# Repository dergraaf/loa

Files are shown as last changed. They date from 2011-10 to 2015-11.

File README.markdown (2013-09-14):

Project Loa
===========

The goal of the project is to develop a powerfull and flexible control board
for robotic (and other) applications.

A microcontroller from the STM32F series from ST is used as the central
processing unit. It is coupled with a Spartan-3 FPGA from Xilinx which will
be used as a powerfull I/O-Expander. With this combination it is possible to
control multiple motors with encoders and other actuators while processing
sensor data and controlling the robot.

For small robots everything will fit into the control board, for big system
the board can act as combined motor controller and sensor preprocessor.
The actual planning etc. can than be outsourced to a faster microcontroller
or PC connected via USB or a fast UART bus.

Naming
------

A "Loa" is a allknowing ghost in Voodoo. The different boards are named
after loas.

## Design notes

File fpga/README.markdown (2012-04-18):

VHDL
====

Structure
---------

File structure goes like this:

    |
    +- modules-\        is for the HDL level code 
    |          |
    |          +- <module name> -\
    |          |                 |
    |                            +- hdl    for HDL sources 
    |                            |
    |                            +- tb     for testbenches
    |
    \- toplevel -\
                 |
                 +- <target> -\
                 |            |
                              +- ISE    ISE Project goes here [^1].
                              |
                              \- ...    implementation files (toplevel.vhd, board.ucf, ..)

[^1]: Only the files really needed like *.xise or *.ise

Naming & Coding Conventions
---------------------------

- All filenames are lower case, names separated by underscores
  - Testbenches end in "_tb.vhd"

- All keywords are lower case!
- Generics are UPPER CASE.

- All signals (except "clk" and "reset") in the port list get the suffix "_p"
- Low active signals should be avoid. If neccessary they get the suffix "_n"
  (or "_np" when they are in the port list).
- Packages get the suffix _pkg

- Always use named association when instantiating sub-modules.

- Use the 'two-process' method whenever possible, see [A structured VHDL design method][two-process]
- Use records types to group associated signals

- Use 3 spaces for indention (Emacs default VHDL style)

[two-process]: www.gaisler.com/doc/vhdl2proc.pdf

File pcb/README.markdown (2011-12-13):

Documentation
=============

Microcontroller selection
-------------------------

For this controller board we wanted to use a Cortex-M3 chip. There are only two
families in wider use at the moment. The STM32F series from ST and the LPC1700
series from NXP.
One goal was that the microcontroller should be be able to control the drive
system of a robot without the FPGA. Therefore it needs to be able to read
four quadrature encoder and control two motors. This leaves only the STM32
series as the LPC1700 features only one quadrature encoder.

Currently there are four different strains within the STM32 series available.
The STM32F103 was the first one. A lot of development boards use controllers
from this series. But it has a quite long and annoying Errata Sheet, some
peripherals don't work with each other. Most important it is not possible to
use CAN and USB at the same time because they share an internal buffer.
After the 103er the 105/107er arrived. Their most important feature is that it
is possible to use CAN and USB at the same time. Some other stuff like the
ethernet interface are not important for us. The peripherals are improved,
leading to a shorter Errata Sheet. Their only drawback comparted to the 103er
series is that they are limited to 256kB Flash compared to a maximum of
1024kB for the 103er. The 256kB Flash might just be to few for the desired
application as a robot controller.

In the last time two new strains appeared. The STM32F200- and the
STM32F400-series. They are improvments of the 105/107er with a slightly
different pinout. Some of the power pins need to be connected differently, all
of the IO-Pins remain the same. Therefore it is possible to create a board
which supports STM32F1xx and STM32F2xx through some solder jumpers.
The STM32F207 are a bit faster (120MHz instead of 72MHz) and provide more Flash
memory (up to 1024kB). The STM32F407 uses an Cortex-M4 instead of the Cortex-M3
of all the other devices. With 150MHz and an integrated FPU it should be again
faster, especially for floating point calculations. The STM32F4xx are pin
compatible to the STM32F2xx.

As the STM32F4xx are to new and are not yet available from distributors like
Farnell we choose the STM32F207. This leaves the options of an upgrade to a
STM32F407 later.

STM32F207
---------

Pin  | Alternate Functions      | Usage on the Board         | Proposed Usage
---- | ------------------------ | -------------------------- | ----------------
PA0  | ADC0/Timer 2.1/Timer 5.1 |                            | Encoder 1
PA1  | ADC1/Timer 2.2/Timer 5.2 |                            | Encoder 1
PA2  | ADC2/Timer 9.1           |                            |     - 
PA3  | ADC3/Timer 9.2           |                            |     - 
PA4  | SPI1 Cs                  | -> FPGA (DIN)              | 
PA5  | SPI1 Sck                 | -> FPGA                    | 
PA6  | SPI1 Miso                | <- FPGA                    | 
PA7  | SPI1 Mosi                | -> FPGA                    | 
PA8  |                          | <- FPGA                    | 
PA9  | USB Vbus                 | <- USB                     | 
PA10 | USB ID                   | <- USB                     | 
PA11 | USB DM                   | <> USB                     | 
PA12 | USB DP                   | <> USB                     | 
PA13 | TMS                      | <- JTAG                    | 
PA14 | TCK                      | <- JTAG                    | 
PA15 | TDI                      | <- JTAG                    | 
---- | ------------------------ | -------------------------- | ----------------
PB0  | ADC8/Timer 3.3           |                            |     - 
PB1  | ADC9/Timer 3.4           |                            |     - 
PB2  | (BOOT1)                  | FPGA_CCLK                  | 
PB3  | TDO                      | -> JTAG                    | 
PB4  | Timer 3.1/TRST           |                            | Encoder 2
PB5  | Timer 3.2                |                            | Encoder 2
PB6  | UART1 Tx                 |                            | -> Upstream
PB7  | UART1 Rx                 |                            | <- Upstream
PB8  | I2C1 Scl                 |                            |     - 
PB9  | I2C1 Sda                 |                            |     - 
PB10 | I2C2 Scl                 |                            |     - 
PB11 | I2C2 Sda                 |                            |     - 
PB12 | SPI2 Cs /CAN2 Rx         |                            |     - 
PB13 | SPI2 Sck/CAN2 Tx         |                            |     - 
PB14 | SPI2 Miso                |                            |     - 
PB15 | SPI2 Mosi                |                            |     - 
---- | ------------------------ | -------------------------- | ----------------
PC0  | ADC10                    |                            |     - 
PC1  | ADC11                    |                            |     - 
PC2  | ADC12                    |                            |     - 
PC3  | ADC13                    |                            |     - 
PC4  | ADC14                    |                            |     - 
PC5  | ADC15                    |                            |     - 
PC6  | Timer 3.1/Timer 8.1      |                            | Encoder 3
PC7  | Timer 3.2/Timer 8.2      |                            | Encoder 3
PC8  | Timer 3.3/Timer 8.3      |                            |     - 
PC9  | Timer 3.4/Timer 8.4      |                            |     - 
PC10 | UART4 Tx                 |                            | SAB (Sensor Actor Bus)
PC11 | UART4 Rx                 |                            | SAB (       "        )
PC12 | UART5 Tx                 |                            | -> Debug UART
PC13 | (nur als Eingang)        | <- Button 1                | 
PC14 | (nur als Eingang)        | <- FPGA (DONE)             | 
PC15 | (nur als Eingang)        | <- SD Card Detect          | 
---- | ------------------------ | -------------------------- | ----------------
PD0  | CAN1 Rx                  | <- CAN                     | 
PD1  | CAN1 Tx                  | -> CAN                     | 
PD2  | UART5 Rx                 |                            | <- Debug UART
PD3  |                          | -> SD Card (CS)            | 
PD4  |                          |                            |     - 
PD5  | UART2 Tx                 |                            | SPI 1
PD6  | UART2 Rx                 |                            | SPI 1
PD7  | UART2 Ck                 |                            | SPI 1
PD8  | UART3 Tx                 | -> SD Card/Dataflash       | 
PD9  | UART3 Rx                 | <- SD Card/Dataflash       | 
PD10 | UART3 Ck                 | -> SD Card/Dataflash       | 
PD11 |                          | -> Dataflash (CS)          | 
PD12 | Timer 4.1                |                            | Encoder 4
PD13 | Timer 4.2                |                            | Encoder 4
PD14 | Timer 4.3                |                            |     - 
PD15 | Timer 4.4                |                            |     - 
---- | ------------------------ | -------------------------- | ----------------
PE0  |                          | -> FPGA (CCLK)             | 
PE1  |                          | -> FPGA (PROG_B)           | 
PE2  |                          | -> FPGA                    | 
PE3  |                          | -> LED0                    | 
PE4  |                          | -> LED1                    | 
PE5  | Timer 9.1                | -> LED2                    | 
PE6  | Timer 9.2                | -> LED3                    | 
PE7  |                          | <- FPGA (INIT_B)           | 
PE8  | Timer 1.1N               |                            | Motor 1
PE9  | Timer 1.1                |                            | Motor 1
PE10 | Timer 1.2N               |                            | Motor 2
PE11 | Timer 1.2                |                            | Motor 2
PE12 | Timer 1.3N               |                            |     - 
PE13 | Timer 1.3                |                            |     - 
PE14 | Timer 1.4                |                            |     - 
PE15 |                          |                            |     - 

#### Peripherals

- 2x Motor (Timer 1)
- 4x Encoder (Timer 3+4+5+8)

- 1x Upstream (Uart 1)
- 1x Debug (Uart 5)
- 2x SPI (Uart2+SPI2)
- 1x Peripheral UART (Uart 4)

#### SPI vs. SDIO

We choose a SPI over the SDIO interface for the SD Card because SDIO would
have blocked UART4 and UART5.

#### JTAG Connector

This is the official JTAG Connector proposed by ARM for the Cortex-M3. The only
difference is that we don't use a 1.27mm grid but a normal 2.54mm one. This
allows to use standard ribbon cable.

            ------
    3.3V --| 1  2 |-- TMS
     GND --| 3  4 |-- TCLK
     GND -[| 5  6 |-- TDO
    RTCK --| 7  8 |-- TDI
     GND --| 9 10 |-- Reset (SRST)
            ------

On this connector TRST (also called NJTRST) is not connected. This might
lead to the problem that the "reset halt" command from OpenOCD doesn't work.

RTCK is only used for ARM7 devices, so it is left open here.

FPGA Spartan-3
--------------

The Spartan-3 was choosen because it was the only FPGA from all the Spartan-3
Series (3,3E,3A,3AN) that is available in TQFP144 package from Reichelt or
Farnell.

The XC3S50A and XC3S50AN are also available, but the bigger packages are not.

### Pins

Unused pins are defined as inputs with pull-downs by default. Can be changed
by primitives or constraints in the bitstream generation.

All user-I/O pins, input-only pins, and dual-purpose pins that are not actively
involved in the currently-selected configuration mode are high impedance
(floating, three-stated, Hi-Z) during the configuration process.

### Configuration of the FPGA

DONE
:   Output with 2,5V supply. Driven low during configuration. Goes high after
    configuration has finished.

PROG_B
:   Input with 2,5 supply. Low pulse (>= 500ns) restarts the configuration
    process.

CCLK
:   Input with 2,5 supply in slave modes. Configuration clock.

DIN
:   Serial Mode input

DOUT
:   Serial Data Output. Not used in single FPGA designs.

INIT_B
:   Output with 3,3V supply. Driven low during before configuration. After it
    goes high the M[2:0] pins are sampled and the configuration is started.
    Holding the pin low stalls the configuration start. During configuration
    the FPGA indicates the occurrence of a configuration
    data error (i.e., CRC error) by asserting INIT_B Low.
    After configuration successfully completes, i.e., when the DONE pin goes
    High, the INIT_B pin is available as a full user-I/O pin.

HSWAP_EN 
:   When the pin is Low, each pin (not only the configuration pins) has an
    internal pull-up resistor that is active throughout configuration, starting
    immediately on power-up.

M[2:0]
:   Select the configuration mode.
    '111' Slave Serial Mode
    '101' JTAG Mode

#### Spartan 3 Bitstream Size

Device  | Configuration
        |  Size [Bits]
------- | --------------
XC3S50  |     439,264
XC3S200 |   1,047,616
XC3S400 |   1,699,136

### Power Supply

http://focus.ti.com/analog/docs/refdesignovw.tsp?familyId=64&contentType=2&genContentId=34823

For the XC3S250E:
- 1.2V at 1A
- 2.5V at 0.15A
- 3.3V at 3A

For the XC3S500E
- 1.2V at 1.5A
- 2.5V at 0.15A
- 3.3V at 3A

The XC3S200/400 should be somewhere in between, the XC3S50 significantly lower.

### JTAG Connector

The JTAG connector is a stripped down version of the original connector from
the Xilinx Parallel Cable IV. Original it uses 14 pins, but we leave the last
four pins out to fit it to a standard 10 pin header. These pins are only used
for programming the FPGA via Slave Serial mode through the PC so no
functionality is lost.

           ------
    GND --| 1  2 |-- Vref (connect to Vaux)
    GND --| 3  4 |-- TMS
    GND -[| 5  6 |-- TCK
    GND --| 7  8 |-- TDO
    GND --| 9 10 |-- TDI
           ------

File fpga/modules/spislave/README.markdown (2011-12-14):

The SPI Slave module has two responsibilities:
- Decoding the SPI protocol
- Busmaster for the internal bus

Protocol
--------

All transfers (address and data) are 16-bit. First the address is written.
The MSB determines wether the folowing transfer is a read (MSB = '0') or write (MSB = '1')
transfer.

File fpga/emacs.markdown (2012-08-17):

Emacs
=====

Install Emacs via:

    $ sudo apt-get install emacs

Commands
--------
 
C => Strg  
M => Alt  

C-c C-b		Beautify Buffer  
C-w 		Cut Text  
M-w			Copy Text  
C-y			Paste Text  
C-space		Set mark  
C-x C-s		Save File  
C-X u		Undo

C-c C-p C-w		Copy entity or component
C-c C-p C-c		Paste as component
C-c C-p C-i		Paste as instance
C-c C-p C-s		Paste as signals

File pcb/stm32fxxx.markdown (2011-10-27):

Pin Assignment
==============

STM32F207
---------

Pin  |  ADC  |    Timer    |   UART   |    SPI    | 
---- | ----- | ----------- | -------- | --------- | 
PA0  | ADC0  | Timer 2/5.1 |          |           | 
PA1  | ADC1  | Timer 2/5.2 |          |           | 
PA2  | ADC2  | Timer 9.1   |          |           | 
PA3  | ADC3  | Timer 9.2   |          |           | 
PA4  |       |             |          | SPI1 Cs   | 
PA5  |       |             |          | SPI1 Sck  | 
PA6  |       |             |          | SPI1 Miso | 
PA7  |       |             |          | SPI1 Mosi | 
PA8  |       |             |          |           | 
PA9  |       |             |          |           | USB Vbus
PA10 |       |             |          |           | USB ID
PA11 |       |             |          |           | USB DM
PA12 |       |             |          |           | USB DP
PA13 |       |             |          |           | TMS
PA14 |       |             |          |           | TCK
PA15 |       |             |          |           | TDI

PB0  | ADC8  | Timer 3.3   |          |           | 
PB1  | ADC9  | Timer 3.4   |          |           | 
PB2  |       |             |          |           | 
PB3  |       |             |          |           | TDO
PB4  |       | Timer 3.1   |          |           | TRST
PB5  |       | Timer 3.2   |          |           | 
PB6  |       |             | UART1 Tx |           | 
PB7  |       |             | UART1 Rx |           | 
PB8  |       |             |          |           | I2C1 Scl
PB9  |       |             |          |           | I2C1 Sda
PB10 |       |             |          |           | I2C2 Scl
PB11 |       |             |          |           | I2C2 Sda
PB12 |       |             |          | SPI2 Cs   | CAN2 Rx
PB13 |       |             |          | SPI2 Sck  | CAN2 Tx
PB14 |       |             |          | SPI2 Miso | 
PB15 |       |             |          | SPI2 Mosi | 

PC0  | ADC10 |             |          |           | 
PC1  | ADC11 |             |          |           | 
PC2  | ADC12 |             |          |           | 
PC3  | ADC13 |             |          |           | 
PC4  | ADC14 |             |          |           | 
PC5  | ADC15 |             |          |           | 
PC6  |       | Timer 3/8.1 |          |           | 
PC7  |       | Timer 3/8.2 |          |           | 
PC8  |       | Timer 3/8.3 |          |           | 
PC9  |       | Timer 3/8.4 |          |           | 
PC10 |       |             | UART4 Tx |           | 
PC11 |       |             | UART4 Rx |           | 
PC12 |       |             | UART5 Tx |           | 
PC13 |       |             |          |           | (nur als Eingang)
PC14 |       |             |          |           | (nur als Eingang)
PC15 |       |             |          |           | (nur als Eingang)

PD0  |       |             |          |           | CAN1 Rx
PD1  |       |             |          |           | CAN1 Tx
PD2  |       |             | UART5 Rx |           | 
PD3  |       |             |          |           | 
PD4  |       |             |          |           | 
PD5  |       |             | UART2 Tx |           | 
PD6  |       |             | UART2 Rx |           | 
PD7  |       |             | UART2 Ck |           | 
PD8  |       |             | UART3 Tx |           | 
PD9  |       |             | UART3 Rx |           | 
PD10 |       |             | UART3 Ck |           | 
PD11 |       |             |          |           | 
PD12 |       | Timer 4.1   |          |           | 
PD13 |       | Timer 4.2   |          |           | 
PD14 |       | Timer 4.3   |          |           | 
PD15 |       | Timer 4.4   |          |           | 

PE0  |       |             |          |           | 
PE1  |       |             |          |           | 
PE2  |       |             |          |           | 
PE3  |       |             |          |           | 
PE4  |       |             |          |           | 
PE5  |       | Timer 9.1   |          |           | 
PE6  |       | Timer 9.2   |          |           | 
PE7  |       |             |          |           | 
PE8  |       | Timer 1.1N  |          |           | 
PE9  |       | Timer 1.1   |          |           | 
PE10 |       | Timer 1.2N  |          |           | 
PE11 |       | Timer 1.2   |          |           | 
PE12 |       | Timer 1.3N  |          |           | 
PE13 |       | Timer 1.3   |          |           | 
PE14 |       | Timer 1.4   |          |           | 
PE15 |       |             |          |           |

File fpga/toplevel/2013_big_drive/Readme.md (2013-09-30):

Configuration Workflow
======================

FPGA connected by JTAG
----------------------

	 VHDL Files, UCF Files
	  |
	  | Xilinx ISE: xst, ngdbuild, map, par, trce, bitgen
	  v
	 ise/toplevel.bit
	  |
	  | Xilinx ISE: impact -batch impact.cmd
	  v
	 ise/toplevel.svf
	  |
	  | UrJTAG: jtag urjtag.cmd
	  v
	 FPGA per JTAG
	 
Configure FPGA by STM32
-----------------------

The configuration must be stored into the external flash. 
There is a java tool

	 VHDL Files, UCF Files
	  |
	  | Xilinx ISE: xst, ngdbuild, map, par, trce, bitgen
	  v
	 ise/toplevel.bit
	  |
	  | 
	  v

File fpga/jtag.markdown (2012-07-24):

Programming an FPGA
===================

The result of the implementation with the synthesis tools from Xilinx is a bit-file. 
This bit-file must be programmed into the FPGA. This can be done by various means:

*   JTAG
*   Platform Flash
*   Microcontroller

See Xilinx documentation for details. Here programming the FPGA using the JTAG port
is describe. Two different tools are tested: UrJtag and xc3sprogram. Both were used 
with the busblaster v2 hardware. 

Using UrJtag
------------

See http://urjtag.sourceforge.net/

### Generate a SVF File

Create a new file called "impact.cmd" with the following content:

    setMode -bs
    setCable -port svf -file toplevel.svf
    addDevice -p 1 -file path/to/your/bitfile.bit
    program -p 1
    closeCable
    quit

Now run impact to create a SVF file:

    $ impact -batch impact.cmd

If the 'impact' command isn't found check that the ISE path is added to PATH.
For example add the following to ~/.bashrc (adapt it your ISE-path):
    export PATH=$PATH:/home/user/fpga/xilinx_ise/ISE_DS/ISE/bin/lin/

### Download and Install

get UrJtag at http://sourceforge.net/projects/urjtag/files/latest/download?source=files

    $ cd urjtag-0.10
    $ ./configure --with-libftdi --enable-lowlevel=ftdi
    $ make
    $ sudo make install

you can also use the git repository:

    $ git clone git://urjtag.git.sourceforge.net/gitroot/urjtag/urjtag urjtag
    $ cd urjtag/urjtag
    $ sudo apt-get install autoconf autopoint libtool libusb-dev libftdi-dev python-dev flex bison
    $ autoreconf -i -s -v -f
    $ ./configure
    $ make
    $ sudo make install

And for Ubuntu users:

    $ sudo su
    $ echo "/usr/local/lib" > /etc/ld.so.conf.d/other.conf
    $ ldconfig
    $ exit

### Connect to your FPGA

    $ jtag
    jtag> cable jtagkey vid=0x0403 pid=0x6010 driver=ftdi-mpsse
    Connected to libftdi driver.
    jtag> detect
    IR length: 6
    Chain length: 1
    Device Id: 00000001010000011100000010010011 (0x000000000141C093)
      Manufacturer: Xilinx
      Part(0):         xc3s400
      Stepping:     0
      Filename:     /usr/local/share/urjtag/xilinx/xc3s400/xc3s400
    jtag> 

### Program the FPGA

    jtag> svf toplevel.svf
    jtag> 

xc3sprog
--------

The benefit of xc3sprog is that it is not necessary to run Xilinx Impact. 
xc3sprog can write bit-files directly to FPGA. 

### Get the latest xc3sprog

The precompiled version did not work. You need cmake and libftdi-dev. 

    $ svn co https://xc3sprog.svn.sourceforge.net/svnroot/xc3sprog xc3sprog

Create a new build directory and dive into

    $ mkdir xc3sprog/build
    $ cd    xc3sprog/build
    $ cmake ../trunk
    $ make

### Test the tool

Now xc3sprog is ready. Make sure you can access the USB device. Adjust 
permissions of /dev/bus/usb/00?/0??.

   $  ./xc3sprog -c bbv2 -j

will show something like

    XC3SPROG (c) 2004-2011 xc3sprog project $Rev: 674 $ OS: Linux
    Free software: If you contribute nothing, expect nothing!
    Feedback on success/failure/enhancement requests:
        http://sourceforge.net/mail/?group_id=170565 
    Check Sourceforge for updates:
        http://sourceforge.net/projects/xc3sprog/develop
    
    Using Libftdi, 
    JTAG loc.:   0  IDCODE: 0x01414093  Desc:                        XC3S200 Rev: A  IR length:  6
    JTAG loc.:   1  IDCODE: 0x05045093  Desc:                         XCF02S Rev: A  IR length:  8

### Write to FPGA

This was a test using the Digilent Spartan 3 Development board. You can write
a bit-file to the FPGA (or with -p 1 to the platform flash) using:

    $ ./xc3sprog -c bbv2 /path/to/your/bitfile.bit

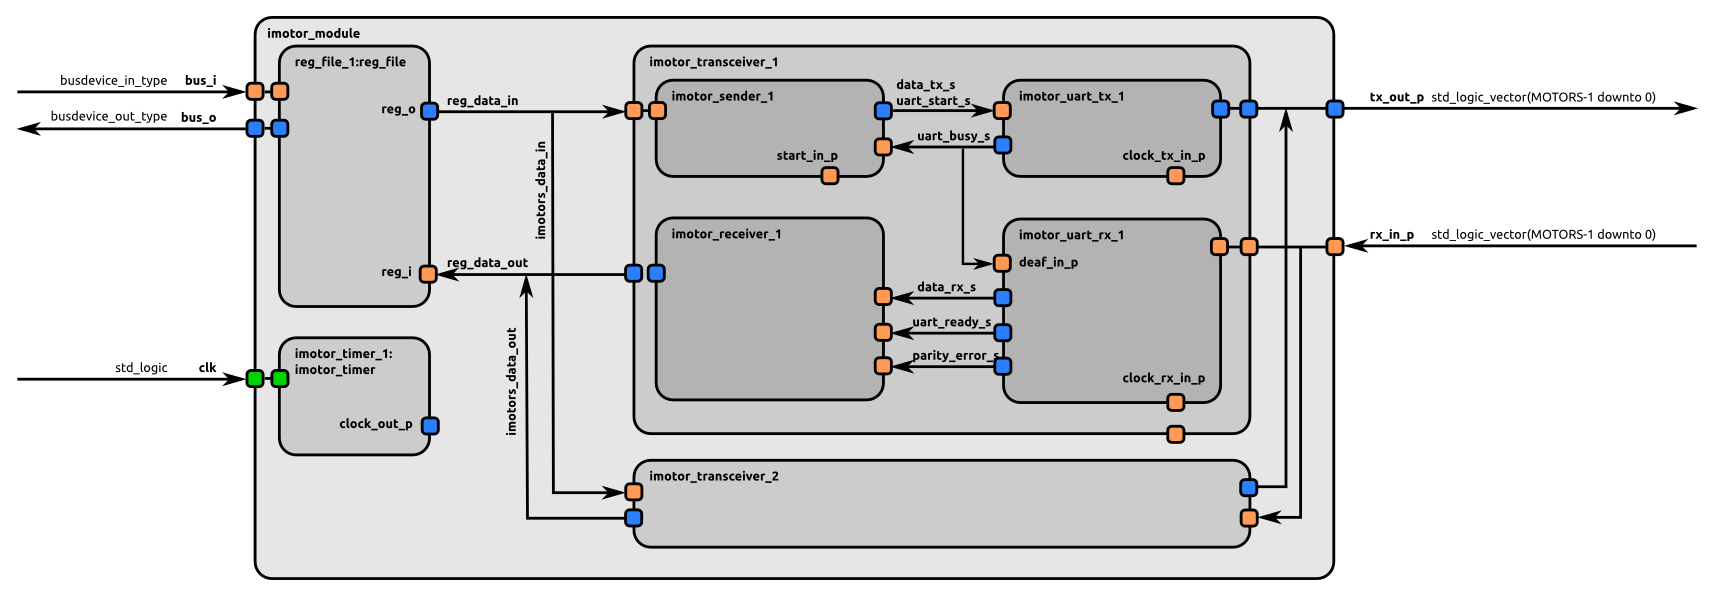
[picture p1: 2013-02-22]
fpga/modules/imotor/doc/imotor_module.png

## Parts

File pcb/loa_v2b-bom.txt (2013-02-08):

// Partlist exported from /home/dhebbeker/rca/loa/pcb/loa_v2b.sch at 08/02/2013 18:54// Partlist exported from /home/dhebbeker/rca/loa/pcb/loa_v2b.sch at 08/02/2013 18:54Source;Ordercode;Quantity;
RCA;auf Lager;1;
Unknown;SJS ;1;
Digikey;732-1800-1-ND (0,68u);2;
Unknown;C-EUC0805 1µ;5;
Unknown;R-EU_R0805 1M;1;
Digikey;399-7834-1ndw (1n);2;
Unknown;C-EUC0805 2u2;2;
Unknown;C-EUC0805 4µ7;1;
Reichelt;L-PISG 4,7µ;1;
Digikey;311-4.99KCRCT-ND (4k99);1;
Digikey;311-1355-1-nd (4u7);1;
Digikey;122-1745-ND (6SLX9TQG144);1;
Digikey;399-1089-1-nd (6n8);1;
Digikey;RMCF0805FT8K06CT-ND (8k06);1;
Unknown;R-EU_R0603 10k;7;
Unknown;C-EUC0603 10n;5;
Reichelt;SMD TAN.22/6,3;3;
Reichelt;SMD TAN.22/20;1;
Unknown;R-EU_R0603 22;2;
Digikey;RMCF0805FT24K9CT-ND  (24k9);1;
Reichelt;XO53 25,00000;1;
Digikey;Y9330CT-ND (33);4;
Reichelt;XO53 50,00000;1;
Unknown;R-EU_R0603 100k;1;
Unknown;C-EUC0603 100n;28;
Unknown;R-EU_R0603 330;5;
Digikey;587-1259-1-nd (470n);2;
Unknown;R-EU_R0805 820;1;
Sample ANALOG;AD7266BSUZ;1;
Reichelt;AT 45DB081D SO;1;
RCA;Sascha;1;
Reichelt;WSL 2X05SMD 2,00;1;
RCA;Sascha;1;
Digikey;MCP1825S-1202E/DB-ND (MCP1825S-1202E/DB);1;
RCA;Sascha;1;
Reichelt;MBRS 140 SMD;1;
Digikey;NCP3170ADR2GOSCT-ND (NCP3170);1;
Unknown;SJ2WS PDR_ON;1;
RCA;Sascha;2;
Reichelt;TASTER 9314;1;
Digikey;WM3295CT-ND (SD_DETECT);1;
Sample ST;stm32f407vgt6;1;
Reichelt;SL 2X32G SMD2,00;1;
Reichelt;SL 2X32G SMD2,00;1;

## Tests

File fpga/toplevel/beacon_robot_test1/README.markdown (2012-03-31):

Bitstream
---------

Size for XC3S200A/AN is 1196128 Bits = 149516 Bytes

Files
-----

bin2c.py

   Generates Bitstream Header for an XC3S200A.

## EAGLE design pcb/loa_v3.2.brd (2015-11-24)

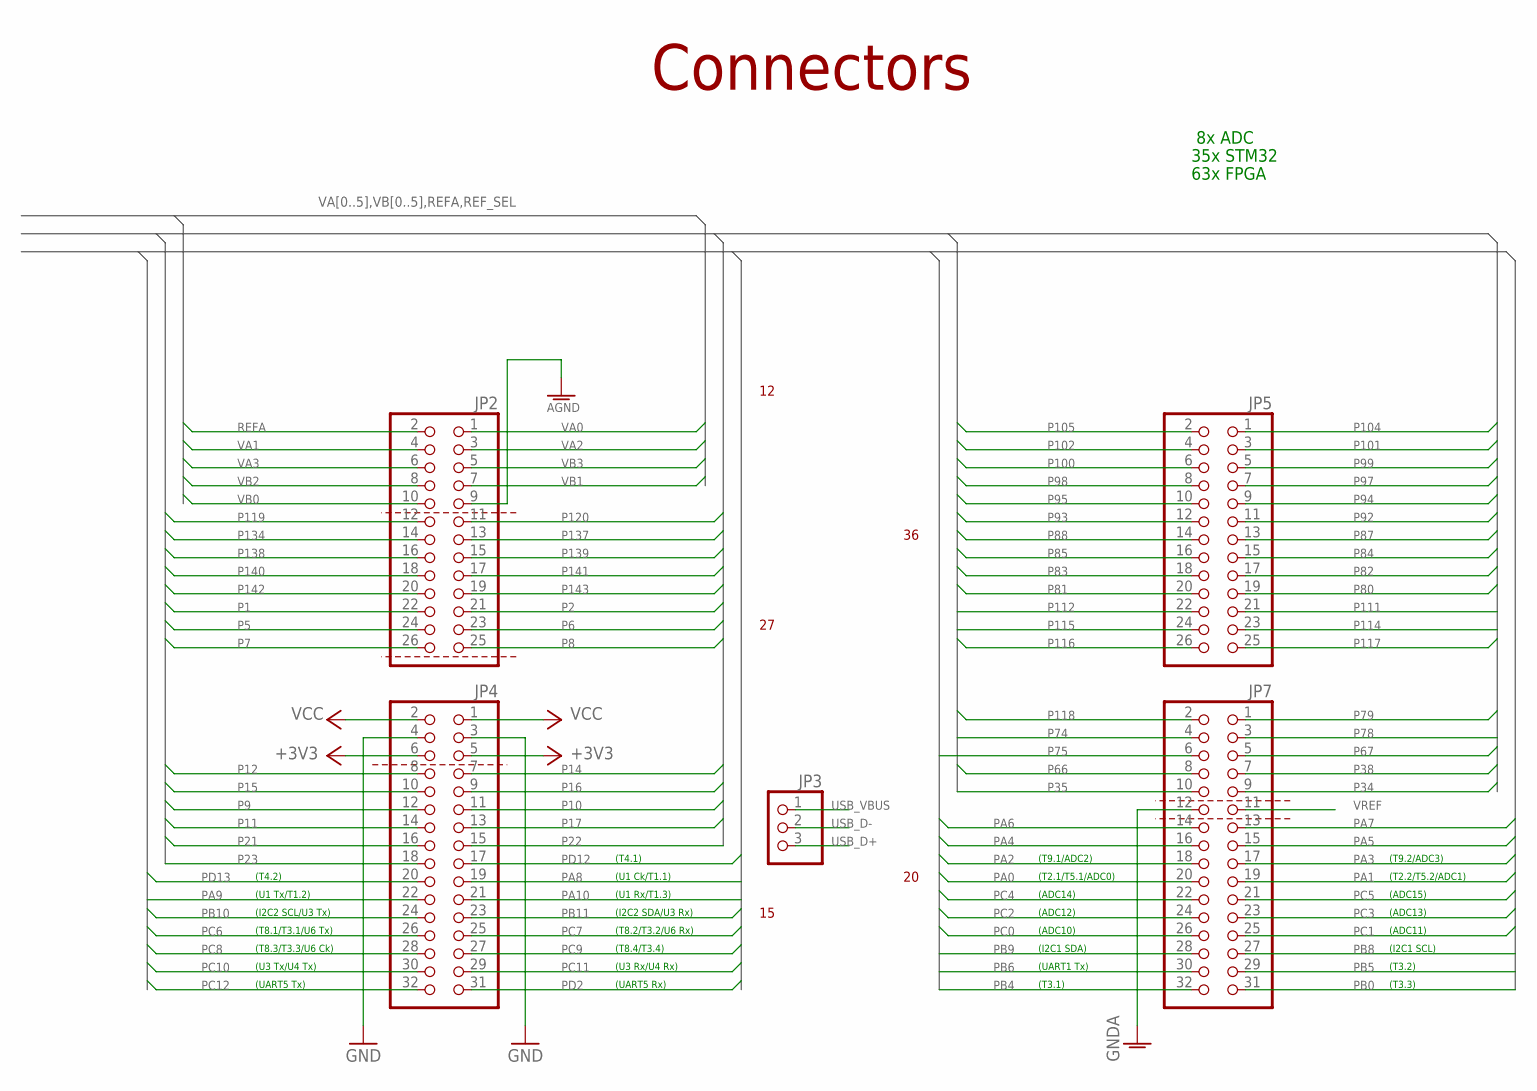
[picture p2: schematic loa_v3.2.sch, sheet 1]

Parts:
JP2, JP5: PINHD-2X13_2.54-SMD; 2X13SMD
JP3: PINHD-1X3_2.54S; 1X03S
JP4, JP7: PINHD-2X16_2.54-SMD; 2X16SMD

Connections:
+3V3: JP4.5, JP4.6; also elsewhere on the board
AGND: JP2.9; also elsewhere on the board
GND: JP4.3, JP4.4; also elsewhere on the board
GNDA: JP7.12; also elsewhere on the board
P1: JP2.22; also elsewhere on the board
P2: JP2.21; also elsewhere on the board
P5: JP2.24; also elsewhere on the board
P6: JP2.23; also elsewhere on the board
P7: JP2.26; also elsewhere on the board
P8: JP2.25; also elsewhere on the board
P9: JP4.12; also elsewhere on the board
P10: JP4.11; also elsewhere on the board
P11: JP4.14; also elsewhere on the board
P12: JP4.8; also elsewhere on the board
P14: JP4.7; also elsewhere on the board
P15: JP4.10; also elsewhere on the board
P16: JP4.9; also elsewhere on the board
P17: JP4.13; also elsewhere on the board
P21: JP4.16; also elsewhere on the board
P22: JP4.15; also elsewhere on the board
P23: JP4.18; also elsewhere on the board
P34: JP7.9; also elsewhere on the board
P35: JP7.10; also elsewhere on the board
P38: JP7.7; also elsewhere on the board
P66: JP7.8; also elsewhere on the board
P67: JP7.5; also elsewhere on the board
P74: JP7.4; also elsewhere on the board
P75: JP7.6; also elsewhere on the board
P78: JP7.3; also elsewhere on the board
P79: JP7.1; also elsewhere on the board
P80: JP5.19; also elsewhere on the board
P81: JP5.20; also elsewhere on the board
P82: JP5.17; also elsewhere on the board
P83: JP5.18; also elsewhere on the board
P84: JP5.15; also elsewhere on the board
P85: JP5.16; also elsewhere on the board
P87: JP5.13; also elsewhere on the board
P88: JP5.14; also elsewhere on the board
P92: JP5.11; also elsewhere on the board
P93: JP5.12; also elsewhere on the board
P94: JP5.9; also elsewhere on the board
P95: JP5.10; also elsewhere on the board
P97: JP5.7; also elsewhere on the board
P98: JP5.8; also elsewhere on the board
P99: JP5.5; also elsewhere on the board
P100: JP5.6; also elsewhere on the board
P101: JP5.3; also elsewhere on the board
P102: JP5.4; also elsewhere on the board
P104: JP5.1; also elsewhere on the board
P105: JP5.2; also elsewhere on the board
P111: JP5.21; also elsewhere on the board
P112: JP5.22; also elsewhere on the board
P114: JP5.23; also elsewhere on the board
P115: JP5.24; also elsewhere on the board
P116: JP5.26; also elsewhere on the board
P117: JP5.25; also elsewhere on the board
P118: JP7.2; also elsewhere on the board
P119: JP2.12; also elsewhere on the board
P120: JP2.11; also elsewhere on the board
P134: JP2.14; also elsewhere on the board
P137: JP2.13; also elsewhere on the board
P138: JP2.16; also elsewhere on the board
P139: JP2.15; also elsewhere on the board
P140: JP2.18; also elsewhere on the board
P141: JP2.17; also elsewhere on the board
P142: JP2.20; also elsewhere on the board
P143: JP2.19; also elsewhere on the board
PA0: JP7.20; also elsewhere on the board
PA1: JP7.19; also elsewhere on the board
PA2: JP7.18; also elsewhere on the board
PA3: JP7.17; also elsewhere on the board
PA4: JP7.16; also elsewhere on the board
PA5: JP7.15; also elsewhere on the board
PA6: JP7.14; also elsewhere on the board
PA7: JP7.13; also elsewhere on the board
PA8: JP4.19; also elsewhere on the board
PA9: JP4.22; also elsewhere on the board
PA10: JP4.21; also elsewhere on the board
PB0: JP7.31; also elsewhere on the board
PB4: JP7.32; also elsewhere on the board
PB5: JP7.29; also elsewhere on the board
PB6: JP7.30; also elsewhere on the board
PB8: JP7.27; also elsewhere on the board
PB9: JP7.28; also elsewhere on the board
PB10: JP4.24; also elsewhere on the board
PB11: JP4.23; also elsewhere on the board
PC0: JP7.26; also elsewhere on the board
PC1: JP7.25; also elsewhere on the board
PC2: JP7.24; also elsewhere on the board
PC3: JP7.23; also elsewhere on the board
PC4: JP7.22; also elsewhere on the board
PC5: JP7.21; also elsewhere on the board
PC6: JP4.26; also elsewhere on the board
PC7: JP4.25; also elsewhere on the board
PC8: JP4.28; also elsewhere on the board
PC9: JP4.27; also elsewhere on the board
PC10: JP4.30; also elsewhere on the board
PC11: JP4.29; also elsewhere on the board
PC12: JP4.32; also elsewhere on the board
PD2: JP4.31; also elsewhere on the board
PD12: JP4.17; also elsewhere on the board
PD13: JP4.20; also elsewhere on the board
REFA: JP2.2; also elsewhere on the board
USB_D+: JP3.3; also elsewhere on the board
USB_D-: JP3.2; also elsewhere on the board
USB_VBUS: JP3.1; also elsewhere on the board
VA0: JP2.1; also elsewhere on the board
VA1: JP2.4; also elsewhere on the board
VA2: JP2.3; also elsewhere on the board
VA3: JP2.6; also elsewhere on the board
VB0: JP2.10; also elsewhere on the board
VB1: JP2.7; also elsewhere on the board
VB2: JP2.8; also elsewhere on the board
VB3: JP2.5; also elsewhere on the board
VCC: JP4.1, JP4.2; also elsewhere on the board
VREF: JP7.11; also elsewhere on the board

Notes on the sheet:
Connectors
(T2.1/T5.1/ADC0)
(T2.2/T5.2/ADC1)
(T9.1/ADC2)
(T9.2/ADC3)
(ADC10)
(ADC11)
(ADC12)
(ADC13)
(ADC14)
(ADC15)
(I2C1 SCL)
(I2C1 SDA)
(UART1 Tx)
(T3.1)
(T3.2)
(UART5 Rx)
(UART5 Tx)
(T8.1/T3.1/U6 Tx)
(T8.2/T3.2/U6 Rx)
(T8.3/T3.3/U6 Ck)
(T8.4/T3.4)
(T4.2)
(T4.1)
(U1 Tx/T1.2)
(U1 Rx/T1.3)
(U1 Ck/T1.1)
(U3 Tx/U4 Tx)
(U3 Rx/U4 Rx)
(I2C2 SDA/U3 Rx)
(I2C2 SCL/U3 Tx)
8x ADC
35x STM32
63x FPGA
(T3.3)

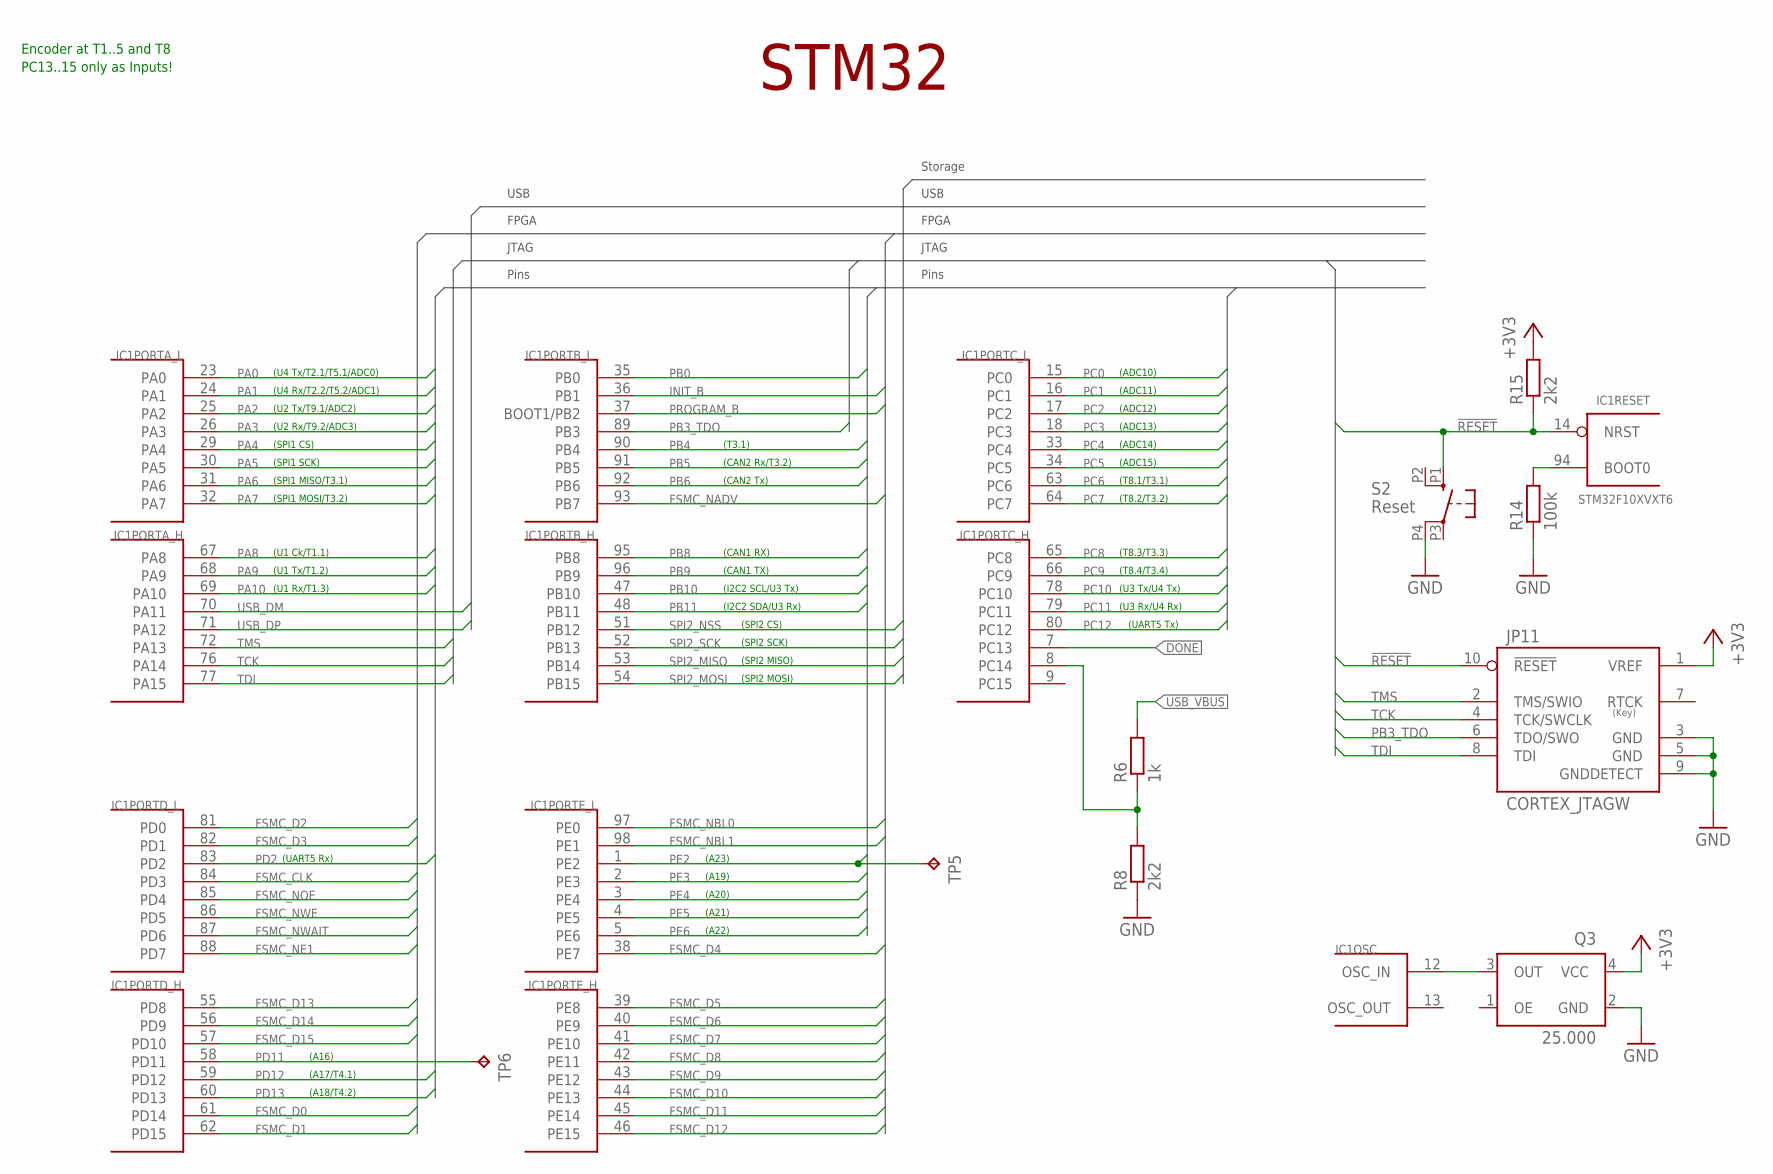
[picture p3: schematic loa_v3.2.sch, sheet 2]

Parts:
IC1: STM32F10XVXT6; TQFP100; DIGIKEY# 497-11605-ND
JP11: CORTEX_JTAGW; ML10
Q3: 25.000; XO53
R6: 1k; R0603
R8, R15: 2k2; R0603
R14: 100k; R0603
S2: Reset; B3F-10XX-SMD
TP5, TP6: TPB1,27; B1,27

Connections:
!RESET: IC1.14 (NRST), JP11.10 (!RESET), R15.1, S2.P1 (S)
+3V3: JP11.1 (VREF), Q3.4 (VCC), R15.2; also elsewhere on the board
DONE: IC1.7 (PC13); also elsewhere on the board
FSMC_CLK: IC1.84 (PD3); also elsewhere on the board
FSMC_D0: IC1.61 (PD14); also elsewhere on the board
FSMC_D1: IC1.62 (PD15); also elsewhere on the board
FSMC_D2: IC1.81 (PD0); also elsewhere on the board
FSMC_D3: IC1.82 (PD1); also elsewhere on the board
FSMC_D4: IC1.38 (PE7); also elsewhere on the board
FSMC_D5: IC1.39 (PE8); also elsewhere on the board
FSMC_D6: IC1.40 (PE9); also elsewhere on the board
FSMC_D7: IC1.41 (PE10); also elsewhere on the board
FSMC_D8: IC1.42 (PE11); also elsewhere on the board
FSMC_D9: IC1.43 (PE12); also elsewhere on the board
FSMC_D10: IC1.44 (PE13); also elsewhere on the board
FSMC_D11: IC1.45 (PE14); also elsewhere on the board
FSMC_D12: IC1.46 (PE15); also elsewhere on the board
FSMC_D13: IC1.55 (PD8); also elsewhere on the board
FSMC_D14: IC1.56 (PD9); also elsewhere on the board
FSMC_D15: IC1.57 (PD10); also elsewhere on the board
FSMC_NADV: IC1.93 (PB7); also elsewhere on the board
FSMC_NBL0: IC1.97 (PE0); also elsewhere on the board
FSMC_NBL1: IC1.98 (PE1); also elsewhere on the board
FSMC_NE1: IC1.88 (PD7); also elsewhere on the board
FSMC_NOE: IC1.85 (PD4); also elsewhere on the board
FSMC_NWAIT: IC1.87 (PD6); also elsewhere on the board
FSMC_NWE: IC1.86 (PD5); also elsewhere on the board
GND: JP11.3 (GND), JP11.5 (GND), JP11.9 (GNDDETECT), Q3.2 (GND), R8.1, R14.1, S2.P4 (P1); also elsewhere on the board
INIT_B: IC1.36 (PB1); also elsewhere on the board
unnamed: IC1.8 (PC14), R6.1, R8.2
unnamed: IC1.94 (BOOT0), R14.2
unnamed: IC1.12 (OSC_IN), Q3.3 (OUT)
PA0: IC1.23 (PA0); also elsewhere on the board
PA1: IC1.24 (PA1); also elsewhere on the board
PA2: IC1.25 (PA2); also elsewhere on the board
PA3: IC1.26 (PA3); also elsewhere on the board
PA4: IC1.29 (PA4); also elsewhere on the board
PA5: IC1.30 (PA5); also elsewhere on the board
PA6: IC1.31 (PA6); also elsewhere on the board
PA7: IC1.32 (PA7); also elsewhere on the board
PA8: IC1.67 (PA8); also elsewhere on the board
PA9: IC1.68 (PA9); also elsewhere on the board
PA10: IC1.69 (PA10); also elsewhere on the board
PB0: IC1.35 (PB0); also elsewhere on the board
PB3_TDO: IC1.89 (PB3), JP11.6 (TDO/SWO)
PB4: IC1.90 (PB4); also elsewhere on the board
PB5: IC1.91 (PB5); also elsewhere on the board
PB6: IC1.92 (PB6); also elsewhere on the board
PB8: IC1.95 (PB8); also elsewhere on the board
PB9: IC1.96 (PB9); also elsewhere on the board
PB10: IC1.47 (PB10); also elsewhere on the board
PB11: IC1.48 (PB11); also elsewhere on the board
PC0: IC1.15 (PC0); also elsewhere on the board
PC1: IC1.16 (PC1); also elsewhere on the board
PC2: IC1.17 (PC2); also elsewhere on the board
PC3: IC1.18 (PC3); also elsewhere on the board
PC4: IC1.33 (PC4); also elsewhere on the board
PC5: IC1.34 (PC5); also elsewhere on the board
PC6: IC1.63 (PC6); also elsewhere on the board
PC7: IC1.64 (PC7); also elsewhere on the board
PC8: IC1.65 (PC8); also elsewhere on the board
PC9: IC1.66 (PC9); also elsewhere on the board
PC10: IC1.78 (PC10); also elsewhere on the board
PC11: IC1.79 (PC11); also elsewhere on the board
PC12: IC1.80 (PC12); also elsewhere on the board
PD2: IC1.83 (PD2); also elsewhere on the board
PD11: IC1.58 (PD11), TP6.TP
PD12: IC1.59 (PD12); also elsewhere on the board
PD13: IC1.60 (PD13); also elsewhere on the board
PE2: IC1.1 (PE2), TP5.TP
PE3: IC1.2 (PE3); also elsewhere on the board
PE4: IC1.3 (PE4); also elsewhere on the board
PE5: IC1.4 (PE5); also elsewhere on the board
PE6: IC1.5 (PE6); also elsewhere on the board
PROGRAM_B: IC1.37 (BOOT1/PB2); also elsewhere on the board
SPI2_MISO: IC1.53 (PB14); also elsewhere on the board
SPI2_MOSI: IC1.54 (PB15); also elsewhere on the board
SPI2_NSS: IC1.51 (PB12); also elsewhere on the board
SPI2_SCK: IC1.52 (PB13); also elsewhere on the board
TCK: IC1.76 (PA14), JP11.4 (TCK/SWCLK)
TDI: IC1.77 (PA15), JP11.8 (TDI)
TMS: IC1.72 (PA13), JP11.2 (TMS/SWIO)
USB_DM: IC1.70 (PA11); also elsewhere on the board
USB_DP: IC1.71 (PA12); also elsewhere on the board
USB_VBUS: R6.2; also elsewhere on the board

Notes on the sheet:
(U4 Tx/T2.1/T5.1/ADC0)
(U4 Rx/T2.2/T5.2/ADC1)
(U2 Tx/T9.1/ADC2)
(U2 Rx/T9.2/ADC3)
(T3.1)
(CAN2 Rx/T3.2)
(CAN1 RX)
(CAN1 TX)
(I2C2 SDA/U3 Rx)
(I2C2 SCL/U3 Tx)
(CAN2 Tx)
(U3 Tx/U4 Tx)
(U3 Rx/U4 Rx)
(UART5 Rx)
STM32
Encoder at T1..5 and T8
(ADC10)
(ADC11)
(ADC12)
(ADC13)
(ADC14)
(ADC15)
(T8.1/T3.1)
(T8.2/T3.2)
(T8.3/T3.3)
(T8.4/T3.4)
PC13..15 only as Inputs!
(UART5 Tx)
(A18/T4.2)
(A17/T4.1)
(A16)
(A23)
(A19)
(A20)
(A21)
(A22)
(U1 Tx/T1.2)
(U1 Rx/T1.3)
(SPI1 CS)
(SPI1 SCK)

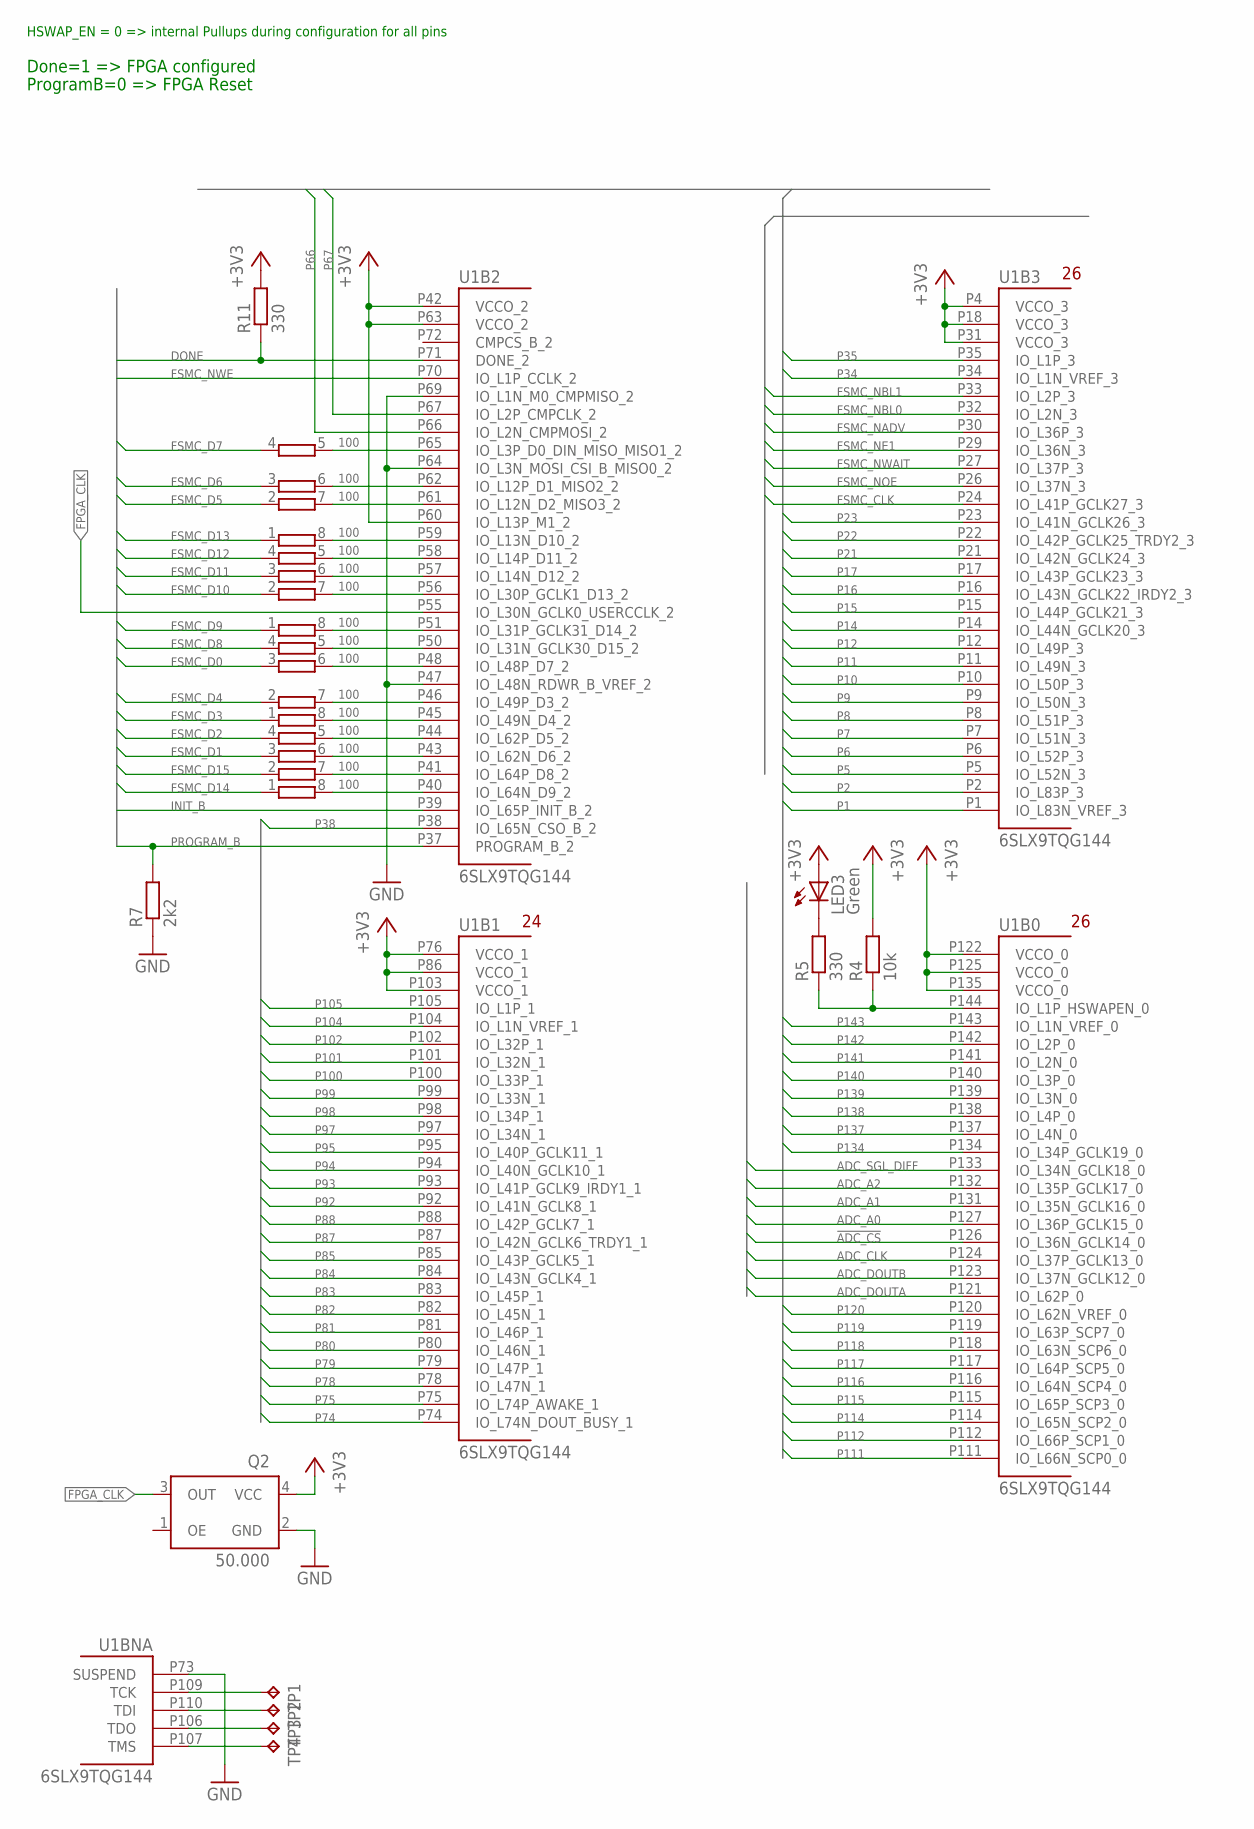
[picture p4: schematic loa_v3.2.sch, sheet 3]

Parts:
LED3: Green; CHIPLED_0805
Q2: 50.000; XO53
R4: 10k; R0603
R5, R11: 330; R0603
R7: 2k2; R0805
RN3, RN4, RN6, RN7: 100; EXB38V
TP1, TP2, TP3, TP4: TPB1,27; B1,27
U1: 6SLX9TQG144; TQ144; DIGIKEY# 122-1745-ND

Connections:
!ADC_CS: U1.P126 (IO_L36N_GCLK14_0); also elsewhere on the board
+3V3: LED3.A, Q2.4 (VCC), R4.2, R11.2, U1.P4 (VCCO_3), U1.P18 (VCCO_3), U1.P31 (VCCO_3), U1.P42 (VCCO_2), U1.P60 (IO_L13P_M1_2), U1.P63 (VCCO_2), U1.P76 (VCCO_1), U1.P86 (VCCO_1), U1.P103 (VCCO_1), U1.P122 (VCCO_0), U1.P125 (VCCO_0), U1.P135 (VCCO_0); also elsewhere on the board
ADC_A0: U1.P127 (IO_L36P_GCLK15_0); also elsewhere on the board
ADC_A1: U1.P131 (IO_L35N_GCLK16_0); also elsewhere on the board
ADC_A2: U1.P132 (IO_L35P_GCLK17_0); also elsewhere on the board
ADC_CLK: U1.P124 (IO_L37P_GCLK13_0); also elsewhere on the board
ADC_DOUTA: U1.P121 (IO_L62P_0); also elsewhere on the board
ADC_DOUTB: U1.P123 (IO_L37N_GCLK12_0); also elsewhere on the board
ADC_SGL_DIFF: U1.P133 (IO_L34N_GCLK18_0); also elsewhere on the board
DONE: R11.1, U1.P71 (DONE_2); also elsewhere on the board
FPGA_CLK: Q2.3 (OUT), U1.P55 (IO_L30N_GCLK0_USERCCLK_2)
FPGA_TCK: TP1.TP, U1.P109 (TCK)
FPGA_TDI: TP2.TP, U1.P110 (TDI)
FPGA_TDO: TP3.TP, U1.P106 (TDO)
FPGA_TMS: TP4.TP, U1.P107 (TMS)
FSMC_CLK: U1.P24 (IO_L41P_GCLK27_3); also elsewhere on the board
FSMC_D0: RN7.3 (1); also elsewhere on the board
FSMC_D1: RN4.3 (1); also elsewhere on the board
FSMC_D2: RN4.4 (1); also elsewhere on the board
FSMC_D3: RN7.1; also elsewhere on the board
FSMC_D4: RN7.2 (1); also elsewhere on the board
FSMC_D5: RN3.2 (1); also elsewhere on the board
FSMC_D6: RN3.3 (1); also elsewhere on the board
FSMC_D7: RN3.4 (1); also elsewhere on the board
FSMC_D8: RN7.4 (1); also elsewhere on the board
FSMC_D9: RN6.1; also elsewhere on the board
FSMC_D10: RN6.2 (1); also elsewhere on the board
FSMC_D11: RN6.3 (1); also elsewhere on the board
FSMC_D12: RN6.4 (1); also elsewhere on the board
FSMC_D13: RN3.1; also elsewhere on the board
FSMC_D14: RN4.1; also elsewhere on the board
FSMC_D15: RN4.2 (1); also elsewhere on the board
FSMC_NADV: U1.P30 (IO_L36P_3); also elsewhere on the board
FSMC_NBL0: U1.P32 (IO_L2N_3); also elsewhere on the board
FSMC_NBL1: U1.P33 (IO_L2P_3); also elsewhere on the board
FSMC_NE1: U1.P29 (IO_L36N_3); also elsewhere on the board
FSMC_NOE: U1.P26 (IO_L37N_3); also elsewhere on the board
FSMC_NWAIT: U1.P27 (IO_L37P_3); also elsewhere on the board
FSMC_NWE: U1.P70 (IO_L1P_CCLK_2); also elsewhere on the board
GND: Q2.2 (GND), R7.1, U1.P47 (IO_L48N_RDWR_B_VREF_2), U1.P64 (IO_L3N_MOSI_CSI_B_MISO0_2), U1.P69 (IO_L1N_M0_CMPMISO_2), U1.P73 (SUSPEND); also elsewhere on the board
INIT_B: U1.P39 (IO_L65P_INIT_B_2); also elsewhere on the board
unnamed: RN3.5 (2), U1.P65 (IO_L3P_D0_DIN_MISO_MISO1_2)
unnamed: RN3.6 (2), U1.P62 (IO_L12P_D1_MISO2_2)
unnamed: RN3.7 (2), U1.P61 (IO_L12N_D2_MISO3_2)
unnamed: RN3.8 (2), U1.P59 (IO_L13N_D10_2)
unnamed: RN6.5 (2), U1.P58 (IO_L14P_D11_2)
unnamed: RN6.6 (2), U1.P57 (IO_L14N_D12_2)
unnamed: RN6.7 (2), U1.P56 (IO_L30P_GCLK1_D13_2)
unnamed: RN6.8 (2), U1.P51 (IO_L31P_GCLK31_D14_2)
unnamed: RN7.5 (2), U1.P50 (IO_L31N_GCLK30_D15_2)
unnamed: RN7.6 (2), U1.P48 (IO_L48P_D7_2)
unnamed: RN7.7 (2), U1.P46 (IO_L49P_D3_2)
unnamed: RN7.8 (2), U1.P45 (IO_L49N_D4_2)
unnamed: RN4.5 (2), U1.P44 (IO_L62P_D5_2)
unnamed: LED3.C, R5.2
unnamed: R4.1, R5.1, U1.P144 (IO_L1P_HSWAPEN_0)
unnamed: RN4.7 (2), U1.P41 (IO_L64P_D8_2)
unnamed: RN4.6 (2), U1.P43 (IO_L62N_D6_2)
unnamed: RN4.8 (2), U1.P40 (IO_L64N_D9_2)
P1: U1.P1 (IO_L83N_VREF_3); also elsewhere on the board
P2: U1.P2 (IO_L83P_3); also elsewhere on the board
P5: U1.P5 (IO_L52N_3); also elsewhere on the board
P6: U1.P6 (IO_L52P_3); also elsewhere on the board
P7: U1.P7 (IO_L51N_3); also elsewhere on the board
P8: U1.P8 (IO_L51P_3); also elsewhere on the board
P9: U1.P9 (IO_L50N_3); also elsewhere on the board
P10: U1.P10 (IO_L50P_3); also elsewhere on the board
P11: U1.P11 (IO_L49N_3); also elsewhere on the board
P12: U1.P12 (IO_L49P_3); also elsewhere on the board
P14: U1.P14 (IO_L44N_GCLK20_3); also elsewhere on the board
P15: U1.P15 (IO_L44P_GCLK21_3); also elsewhere on the board
P16: U1.P16 (IO_L43N_GCLK22_IRDY2_3); also elsewhere on the board
P17: U1.P17 (IO_L43P_GCLK23_3); also elsewhere on the board
P21: U1.P21 (IO_L42N_GCLK24_3); also elsewhere on the board
P22: U1.P22 (IO_L42P_GCLK25_TRDY2_3); also elsewhere on the board
P23: U1.P23 (IO_L41N_GCLK26_3); also elsewhere on the board
P34: U1.P34 (IO_L1N_VREF_3); also elsewhere on the board
P35: U1.P35 (IO_L1P_3); also elsewhere on the board
P38: U1.P38 (IO_L65N_CSO_B_2); also elsewhere on the board
P66: U1.P66 (IO_L2N_CMPMOSI_2); also elsewhere on the board
P67: U1.P67 (IO_L2P_CMPCLK_2); also elsewhere on the board
P74: U1.P74 (IO_L74N_DOUT_BUSY_1); also elsewhere on the board
P75: U1.P75 (IO_L74P_AWAKE_1); also elsewhere on the board
P78: U1.P78 (IO_L47N_1); also elsewhere on the board
P79: U1.P79 (IO_L47P_1); also elsewhere on the board
P80: U1.P80 (IO_L46N_1); also elsewhere on the board
P81: U1.P81 (IO_L46P_1); also elsewhere on the board
P82: U1.P82 (IO_L45N_1); also elsewhere on the board
P83: U1.P83 (IO_L45P_1); also elsewhere on the board
P84: U1.P84 (IO_L43N_GCLK4_1); also elsewhere on the board
P85: U1.P85 (IO_L43P_GCLK5_1); also elsewhere on the board
P87: U1.P87 (IO_L42N_GCLK6_TRDY1_1); also elsewhere on the board
P88: U1.P88 (IO_L42P_GCLK7_1); also elsewhere on the board
P92: U1.P92 (IO_L41N_GCLK8_1); also elsewhere on the board
P93: U1.P93 (IO_L41P_GCLK9_IRDY1_1); also elsewhere on the board
P94: U1.P94 (IO_L40N_GCLK10_1); also elsewhere on the board
P95: U1.P95 (IO_L40P_GCLK11_1); also elsewhere on the board
P97: U1.P97 (IO_L34N_1); also elsewhere on the board
P98: U1.P98 (IO_L34P_1); also elsewhere on the board
P99: U1.P99 (IO_L33N_1); also elsewhere on the board
P100: U1.P100 (IO_L33P_1); also elsewhere on the board
P101: U1.P101 (IO_L32N_1); also elsewhere on the board
P102: U1.P102 (IO_L32P_1); also elsewhere on the board
P104: U1.P104 (IO_L1N_VREF_1); also elsewhere on the board
P105: U1.P105 (IO_L1P_1); also elsewhere on the board
P111: U1.P111 (IO_L66N_SCP0_0); also elsewhere on the board
P112: U1.P112 (IO_L66P_SCP1_0); also elsewhere on the board
P114: U1.P114 (IO_L65N_SCP2_0); also elsewhere on the board
P115: U1.P115 (IO_L65P_SCP3_0); also elsewhere on the board
P116: U1.P116 (IO_L64N_SCP4_0); also elsewhere on the board
P117: U1.P117 (IO_L64P_SCP5_0); also elsewhere on the board
P118: U1.P118 (IO_L63N_SCP6_0); also elsewhere on the board
P119: U1.P119 (IO_L63P_SCP7_0); also elsewhere on the board
P120: U1.P120 (IO_L62N_VREF_0); also elsewhere on the board
P134: U1.P134 (IO_L34P_GCLK19_0); also elsewhere on the board
P137: U1.P137 (IO_L4N_0); also elsewhere on the board
P138: U1.P138 (IO_L4P_0); also elsewhere on the board
P139: U1.P139 (IO_L3N_0); also elsewhere on the board
P140: U1.P140 (IO_L3P_0); also elsewhere on the board
P141: U1.P141 (IO_L2N_0); also elsewhere on the board
P142: U1.P142 (IO_L2P_0); also elsewhere on the board
P143: U1.P143 (IO_L1N_VREF_0); also elsewhere on the board
PROGRAM_B: R7.2, U1.P37 (PROGRAM_B_2); also elsewhere on the board

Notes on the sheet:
Done=1 => FPGA configured
ProgramB=0 => FPGA Reset
HSWAP_EN = 0 => internal Pullups during configuration for all pins

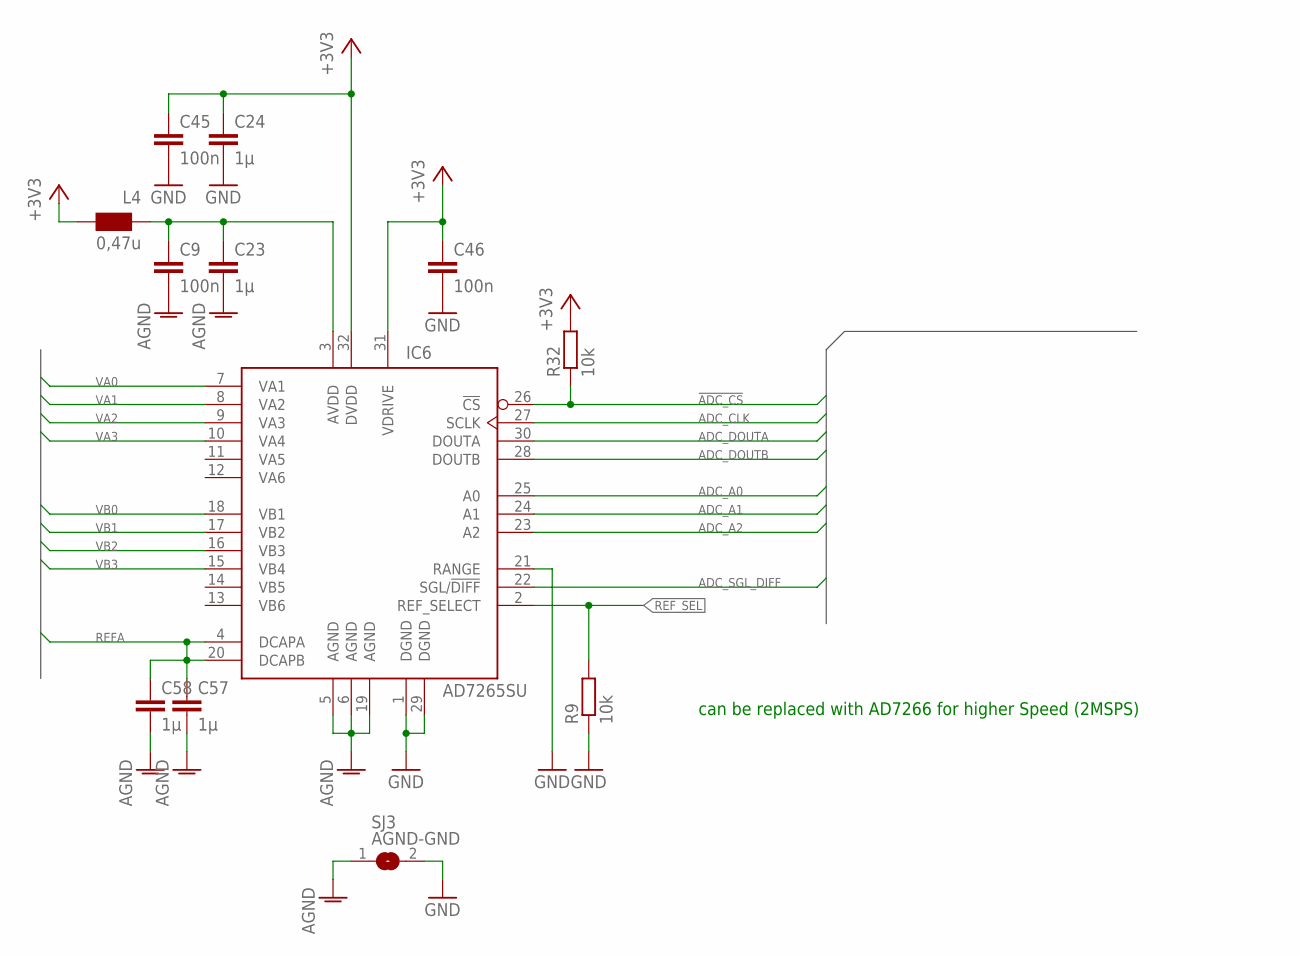
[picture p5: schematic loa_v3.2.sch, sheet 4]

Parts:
C9, C45, C46: 100n; C0603
C23, C24, C57, C58: 1µ; C0805
IC6: AD7265SU; TQFP32-08; DIGIKEY# AD7265BSUZ-ND
L4: 0,47u; WE-KI_0805_B
R9, R32: 10k; R0603
SJ3: AGND-GND; SJS

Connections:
!ADC_CS: IC6.26 (!CS), R32.1; also elsewhere on the board
+3V3: C24.1, C45.1, C46.1, IC6.31 (VDRIVE), IC6.32 (DVDD), L4.1 (2), R32.2; also elsewhere on the board
ADC_A0: IC6.25 (A0); also elsewhere on the board
ADC_A1: IC6.24 (A1); also elsewhere on the board
ADC_A2: IC6.23 (A2); also elsewhere on the board
ADC_CLK: IC6.27 (SCLK); also elsewhere on the board
ADC_DOUTA: IC6.30 (DOUTA); also elsewhere on the board
ADC_DOUTB: IC6.28 (DOUTB); also elsewhere on the board
ADC_SGL_DIFF: IC6.22 (SGL/!DIFF); also elsewhere on the board
AGND: C9.2, C23.2, C57.2, C58.2, IC6.5 (AGND), IC6.6 (AGND), IC6.19 (AGND), SJ3.1; also elsewhere on the board
GND: C24.2, C45.2, C46.2, IC6.1 (DGND), IC6.21 (RANGE), IC6.29 (DGND), R9.1, SJ3.2; also elsewhere on the board
unnamed: C9.1, C23.1, IC6.3 (AVDD), L4.2 (1)
REFA: C57.1, C58.1, IC6.4 (DCAPA), IC6.20 (DCAPB); also elsewhere on the board
REF_SEL: IC6.2 (REF_SELECT), R9.2
VA0: IC6.7 (VA1); also elsewhere on the board
VA1: IC6.8 (VA2); also elsewhere on the board
VA2: IC6.9 (VA3); also elsewhere on the board
VA3: IC6.10 (VA4); also elsewhere on the board
VB0: IC6.18 (VB1); also elsewhere on the board
VB1: IC6.17 (VB2); also elsewhere on the board
VB2: IC6.16 (VB3); also elsewhere on the board
VB3: IC6.15 (VB4); also elsewhere on the board

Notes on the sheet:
can be replaced with AD7266 for higher Speed (2MSPS)

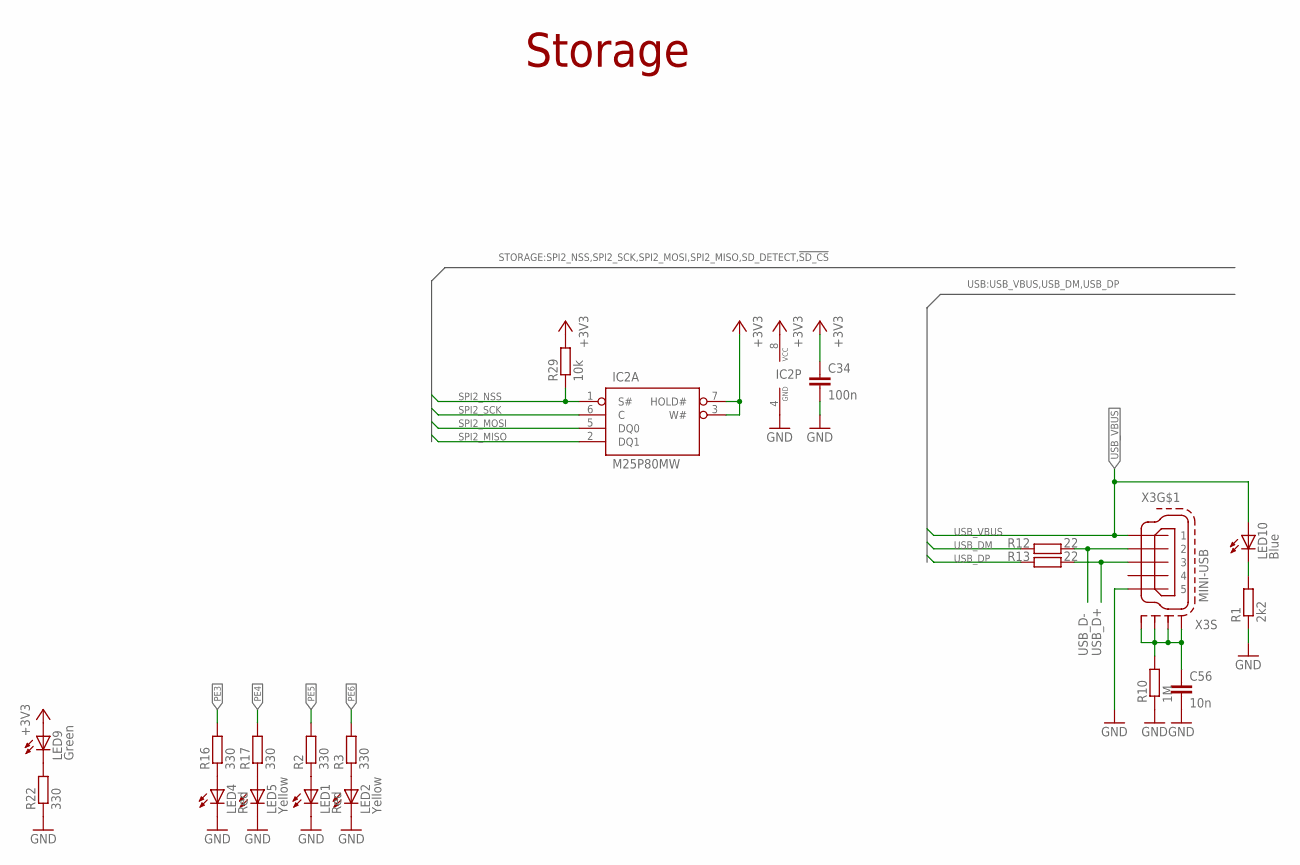
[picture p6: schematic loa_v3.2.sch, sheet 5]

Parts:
C34: 100n; C0603
C56: 10n; C0603
IC2: M25P80MW; SO-08M; DIGIKEY# M25P80-VMN6TPCT-ND
LED1, LED4: Red; CHIPLED_0805
LED2, LED5: Yellow; CHIPLED_0805
LED9: Green; CHIPLED_0805
LED10: Blue; CHIPLED_0805
R1: 2k2; R0805
R2, R3, R16, R17, R22: 330; R0603
R10: 1M; R0805
R12, R13: 22; R0603
R29: 10k; R0603
X3: MINI-USB; 32005-201

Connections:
+3V3: C34.1, IC2.3 (W#), IC2.7 (HOLD#), IC2.8 (VCC), LED9.A, R29.2; also elsewhere on the board
GND: C34.2, C56.2, IC2.4 (GND), LED1.C, LED2.C, LED4.C, LED5.C, R1.1, R10.1, R22.1, X3.5; also elsewhere on the board
unnamed: LED1.A, R2.1
unnamed: LED4.A, R16.1
unnamed: LED2.A, R3.1
unnamed: LED5.A, R17.1
unnamed: LED9.C, R22.2
unnamed: LED10.C, R1.2
unnamed: C56.1, R10.2, X3.M1 (S1), X3.M2 (S2), X3.M3 (S3), X3.M4 (S4)
PE3: R16.2; also elsewhere on the board
PE4: R17.2; also elsewhere on the board
PE5: R2.2; also elsewhere on the board
PE6: R3.2; also elsewhere on the board
SPI2_MISO: IC2.2 (DQ1); also elsewhere on the board
SPI2_MOSI: IC2.5 (DQ0); also elsewhere on the board
SPI2_NSS: IC2.1 (S#), R29.1; also elsewhere on the board
SPI2_SCK: IC2.6 (C); also elsewhere on the board
USB_D+: R13.2, X3.3; also elsewhere on the board
USB_D-: R12.2, X3.2; also elsewhere on the board
USB_DM: R12.1; also elsewhere on the board
USB_DP: R13.1; also elsewhere on the board
USB_VBUS: LED10.A, X3.1; also elsewhere on the board

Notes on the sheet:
Storage

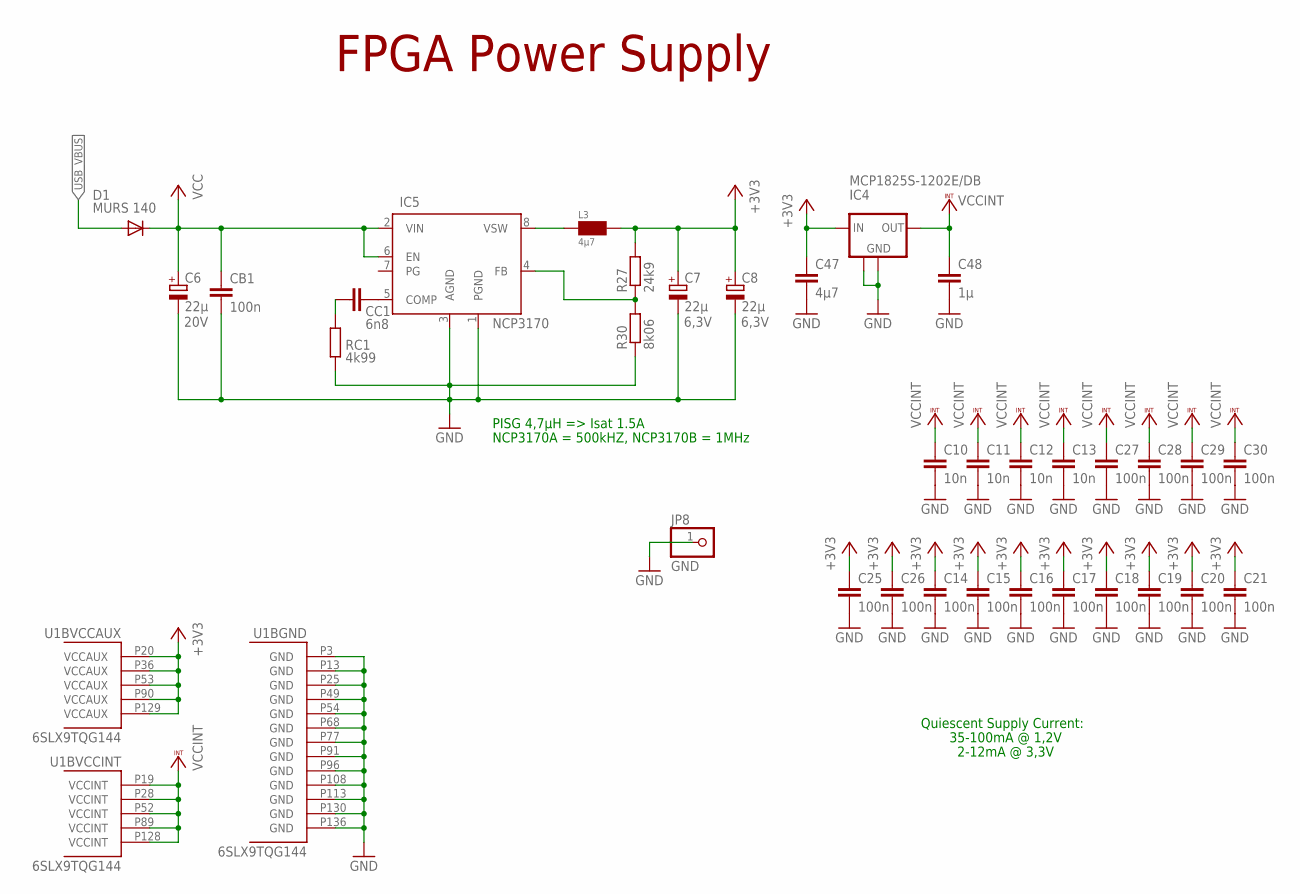
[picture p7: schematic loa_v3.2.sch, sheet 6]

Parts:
C6: 22µ; SMC_D; VOLTAGE 20V
C7, C8: 22µ; SMC_C; VOLTAGE 6,3V
C10, C11, C12, C13: 10n; C0603
C14, C15, C16, C17, C18, C19, C20, C21, C25, C26, C27, C28, C29, C30: 100n; C0603
C47: 4µ7; C0805
C48: 1µ; C0805
CB1: 100n; C0603
CC1: 6n8; C0805
D1: MURS 140; SMB
IC4: MCP1825S-1202E/DB; SOT223; DIGIKEY# MCP1825S-1202E/DB-ND
IC5: NCP3170; SO08; DIGIKEY# NCP3170ADR2GOSCT-ND
JP8: GND; 1X01
L3: 4µ7; L-PISG
R27: 24k9; M0805; DIGIKEY# 311-24.9KCRCT-ND
R30: 8k06; M0805; DIGIKEY# 311-8.06KCRCT-ND
RC1: 4k99; M0805; DIGIKEY# 311-4.99KCRCT-ND
U1: 6SLX9TQG144; TQ144; DIGIKEY# 122-1745-ND

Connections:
+3V3: C7.+, C8.+, C14.1, C15.1, C16.1, C17.1, C18.1, C19.1, C20.1, C21.1, C25.1, C26.1, C47.1, IC4.1 (IN), L3.2, R27.2, U1.P20 (VCCAUX), U1.P36 (VCCAUX), U1.P53 (VCCAUX), U1.P90 (VCCAUX), U1.P129 (VCCAUX); also elsewhere on the board
GND: C6.-, C7.-, C8.-, C10.2, C11.2, C12.2, C13.2, C14.2, C15.2, C16.2, C17.2, C18.2, C19.2, C20.2, C21.2, C25.2, C26.2, C27.2, C28.2, C29.2, C30.2, C47.2, C48.2, CB1.2, IC4.2 (GND), IC4.4 (GND), IC5.1 (PGND), IC5.3 (AGND), JP8.1, R30.1, RC1.1, U1.P3 (GND), U1.P13 (GND), U1.P25 (GND), U1.P49 (GND), U1.P54 (GND), U1.P68 (GND), U1.P77 (GND), U1.P91 (GND), U1.P96 (GND), U1.P108 (GND), U1.P113 (GND), U1.P130 (GND), U1.P136 (GND); also elsewhere on the board
unnamed: CC1.2, RC1.2
unnamed: CC1.1, IC5.5 (COMP)
unnamed: IC5.8 (VSW), L3.1
unnamed: IC5.4 (FB), R27.1, R30.2
USB_VBUS: D1.A; also elsewhere on the board
VCC: C6.+, CB1.1, D1.C, IC5.2 (VIN), IC5.6 (EN); also elsewhere on the board
VCCINT: C10.1, C11.1, C12.1, C13.1, C27.1, C28.1, C29.1, C30.1, C48.1, IC4.3 (OUT), U1.P19 (VCCINT), U1.P28 (VCCINT), U1.P52 (VCCINT), U1.P89 (VCCINT), U1.P128 (VCCINT)

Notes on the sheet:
35-100mA @ 1,2V
Quiescent Supply Current:
2-12mA @ 3,3V
FPGA Power Supply
PISG 4,7µH => Isat 1.5A
NCP3170A = 500kHZ, NCP3170B = 1MHz

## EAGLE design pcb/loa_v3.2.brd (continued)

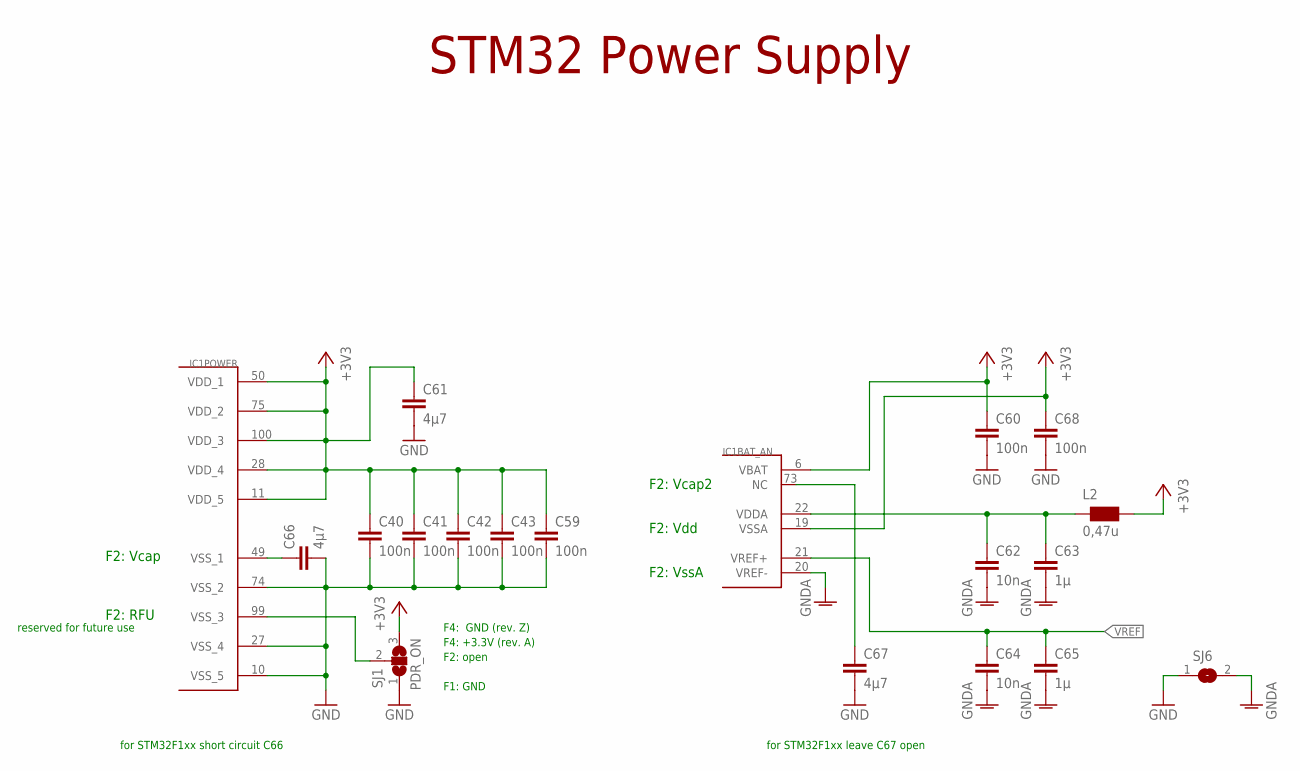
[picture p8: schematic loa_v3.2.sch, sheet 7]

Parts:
C40, C41, C42, C43, C59, C60, C68: 100n; C0603
C61, C66, C67: 4µ7; C0805
C62, C64: 10n; C0603
C63, C65: 1µ; C0805
IC1: STM32F10XVXT6; TQFP100; DIGIKEY# 497-11605-ND
L2: 0,47u; WE-KI_0805_B
SJ1: PDR_ON; SJ_2S
SJ6: SJS

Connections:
+3V3: C40.1, C41.1, C42.1, C43.1, C59.1, C60.1, C61.1, C68.1, IC1.6 (VBAT), IC1.11 (VDD_5), IC1.19 (VSSA), IC1.28 (VDD_4), IC1.50 (VDD_1), IC1.75 (VDD_2), IC1.100 (VDD_3), L2.1 (2), SJ1.3; also elsewhere on the board
GND: C40.2, C41.2, C42.2, C43.2, C59.2, C60.2, C61.2, C66.2, C67.2, C68.2, IC1.10 (VSS_5), IC1.27 (VSS_4), IC1.74 (VSS_2), SJ1.1, SJ6.1; also elsewhere on the board
GNDA: C62.2, C63.2, C64.2, C65.2, IC1.20 (VREF-), SJ6.2; also elsewhere on the board
unnamed: IC1.99 (VSS_3), SJ1.2
unnamed: C66.1, IC1.49 (VSS_1)
unnamed: C67.1, IC1.73 (NC)
VDDA: C62.1, C63.1, IC1.22 (VDDA), L2.2 (1)
VREF: C64.1, C65.1, IC1.21 (VREF+); also elsewhere on the board

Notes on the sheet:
F2: Vcap
F2: RFU
F2: Vdd
F2: VssA
F2: Vcap2
STM32 Power Supply
for STM32F1xx short circuit C66
reserved for future use
for STM32F1xx leave C67 open
F1: GND
F2: open
F4: +3.3V (rev. A)
F4: GND (rev. Z)

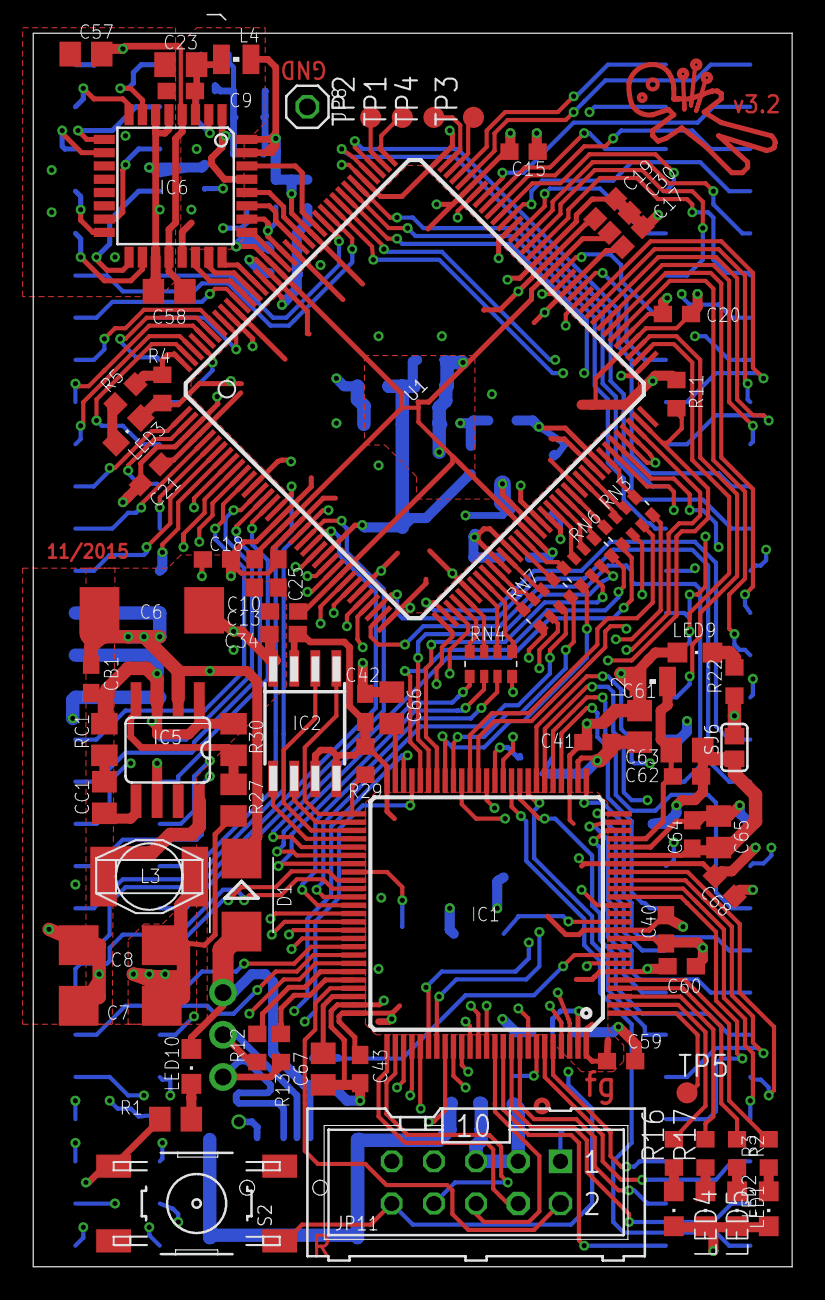
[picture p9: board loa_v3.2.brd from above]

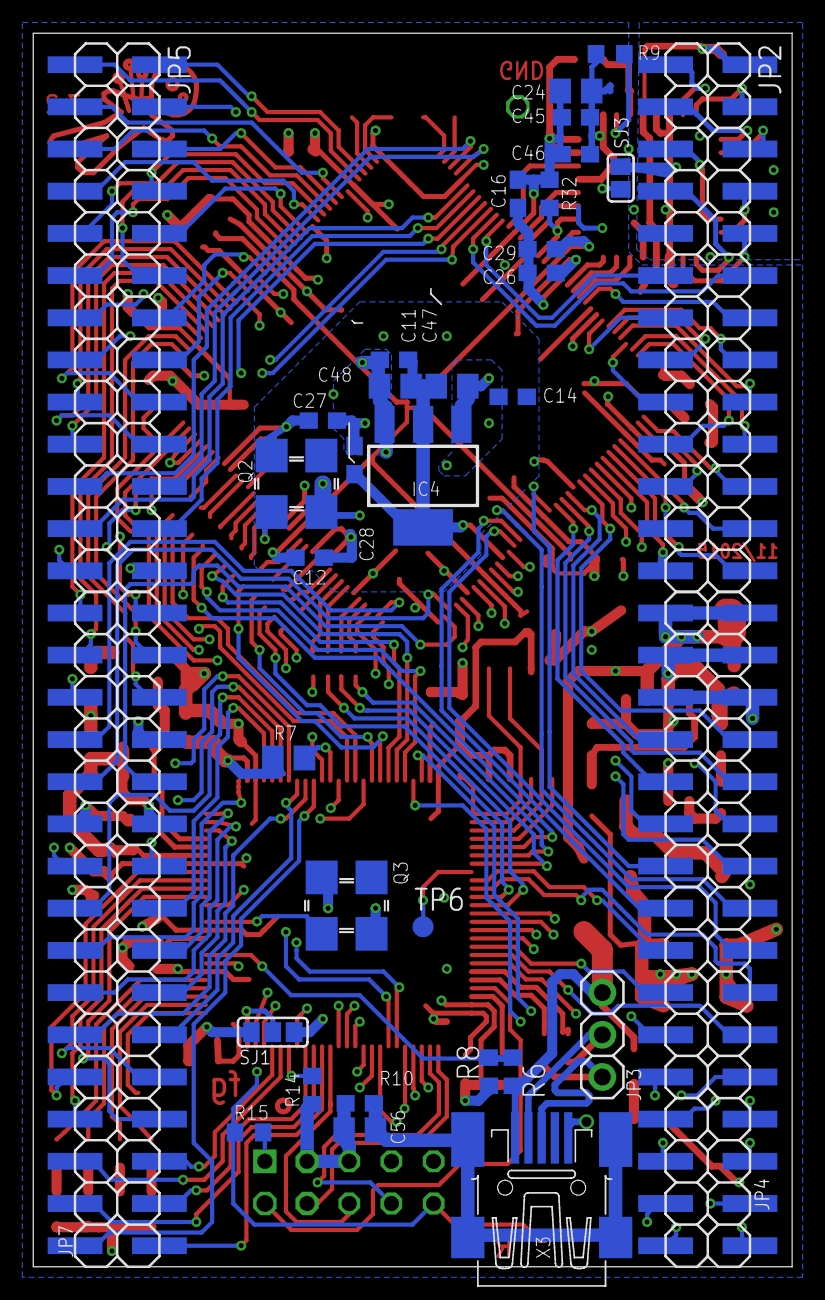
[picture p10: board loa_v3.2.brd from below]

Board: 4 copper layers, 45.7 x 74.3 mm, 112 parts (34 on the bottom side), 212 nets.

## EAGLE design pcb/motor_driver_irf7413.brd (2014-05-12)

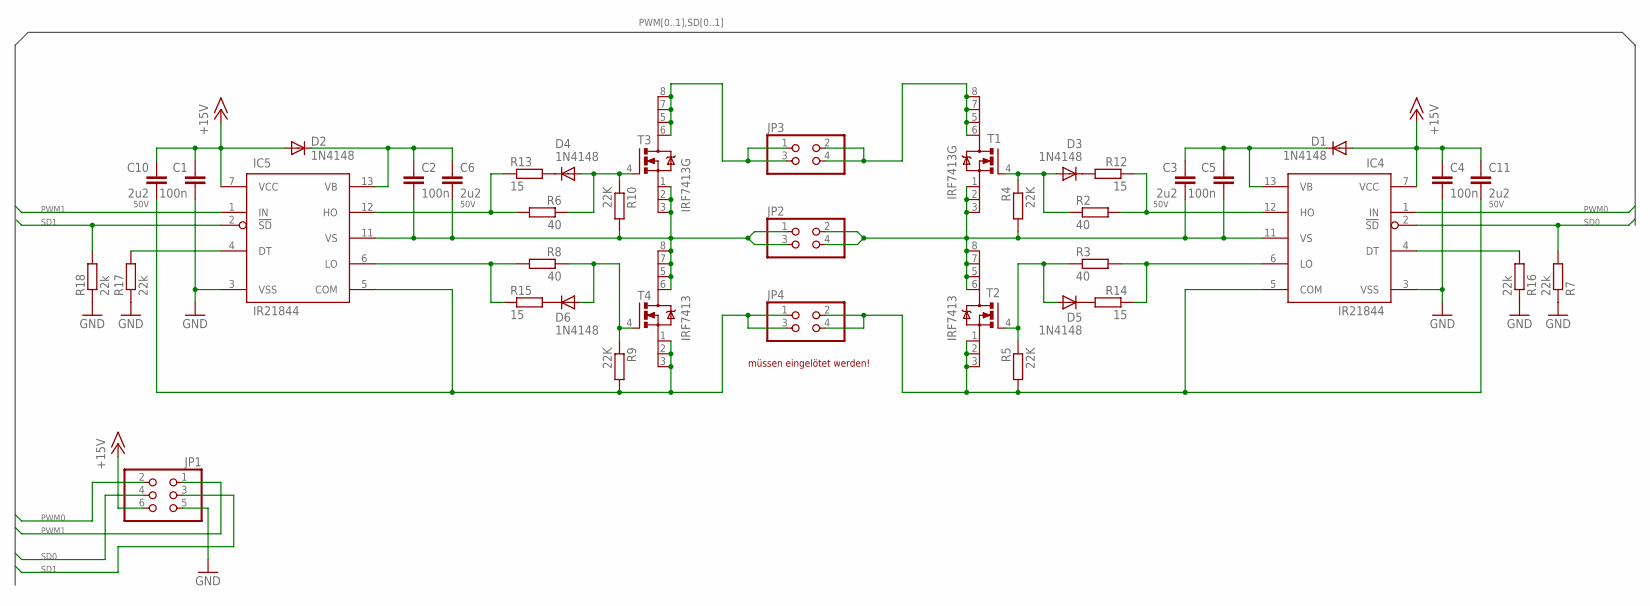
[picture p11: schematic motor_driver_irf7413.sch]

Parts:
C1, C4: 100n; C0805
C2, C5: 100n; C1206
C3, C6, C10, C11: 2u2; C1206; VOLTAGE 50V
D1, D2, D3, D4, D5, D6: 1N4148; SOD80C
IC4, IC5: IR21844; SO14
JP1: PINHD-2X3_2.54-SIDE; 2X03_SIDE
JP2, JP3, JP4: PINHD-2X2_2.54-SIDE; 2X02_SIDE
R2, R3, R6, R8: 40; M0805
R4, R5, R9, R10: 22K; M0805
R7, R16, R17, R18: 22k; M0805
R12, R13, R14, R15: 15; M0805
T1, T3: IRF7413G; SO08G
T2, T4: IRF7413; SO08

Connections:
+15V: C1.1, C4.1, C10.1, C11.1, D1.A, D2.A, IC4.7 (VCC), IC5.7 (VCC), JP1.6
DT0: IC4.4 (DT), R16.2
DT1: IC5.4 (DT), R17.2
GND: C1.2, C4.2, IC4.3 (VSS), IC5.3 (VSS), JP1.5, R7.1, R16.1, R17.1, R18.1
unnamed: C2.2, C6.2, IC5.11 (VS), JP2.1, JP2.3, R10.2, T3.1 (S), T3.2 (S1), T3.3 (S2), T4.5 (D), T4.6 (D1), T4.7 (D2), T4.8 (D3)
unnamed: C3.2, C5.2, IC4.11 (VS), JP2.2, JP2.4, R4.2, T1.1 (S), T1.2 (S1), T1.3 (S2), T2.5 (D), T2.6 (D1), T2.7 (D2), T2.8 (D3)
unnamed: D3.A, R2.1, R4.1, T1.4 (G)
unnamed: D4.A, R6.1, R10.1, T3.4 (G)
unnamed: IC4.12 (HO), R2.2, R12.1
unnamed: IC5.12 (HO), R6.2, R13.1
unnamed: IC5.6 (LO), R8.2, R15.1
unnamed: C2.1, C6.1, D2.C, IC5.13 (VB)
unnamed: D3.C, R12.2
unnamed: D6.A, R8.1, R9.1, T4.4 (G)
unnamed: D4.C, R13.2
unnamed: IC4.6 (LO), R3.2, R14.1
unnamed: D5.A, R3.1, R5.1, T2.4 (G)
unnamed: JP3.1, JP3.3, T3.5 (D), T3.6 (D1), T3.7 (D2), T3.8 (D3)
unnamed: D5.C, R14.2
unnamed: D6.C, R15.2
unnamed: JP3.2, JP3.4, T1.5 (D), T1.6 (D1), T1.7 (D2), T1.8 (D3)
unnamed: C10.2, IC5.5 (COM), JP4.1, JP4.3, R9.2, T4.1 (S), T4.2 (S1), T4.3 (S2)
unnamed: C11.2, IC4.5 (COM), JP4.2, JP4.4, R5.2, T2.1 (S), T2.2 (S1), T2.3 (S2)
unnamed: C3.1, C5.1, D1.C, IC4.13 (VB)
PWM0: IC4.1 (IN), JP1.2
PWM1: IC5.1 (IN), JP1.1
SD0: IC4.2 (!SD), JP1.4, R7.2
SD1: IC5.2 (!SD), JP1.3, R18.2

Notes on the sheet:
müssen eingelötet werden!

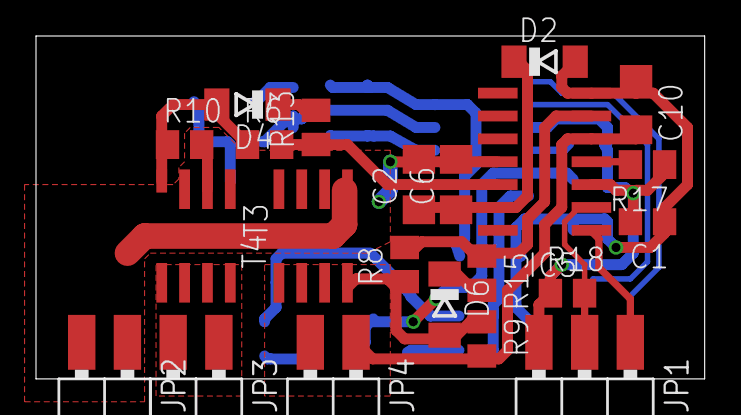
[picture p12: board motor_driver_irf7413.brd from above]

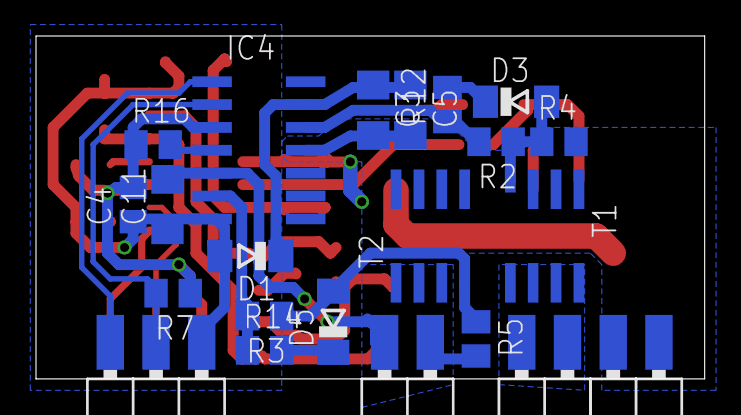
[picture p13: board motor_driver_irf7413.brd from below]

Board: 2 copper layers, 37.1 x 19.1 mm, 40 parts (18 on the bottom side), 28 nets.

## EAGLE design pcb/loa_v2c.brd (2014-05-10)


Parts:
JP7: right; 2X32M_SMD
JP8: left; 2X32M_SMD

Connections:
+3V3: JP7.35, JP7.36; also elsewhere on the board
AGND: JP8.15, JP8.16; also elsewhere on the board
GND: JP7.37, JP7.38, JP8.35, JP8.36; also elsewhere on the board
GNDA: JP7.40; also elsewhere on the board
P1: JP8.30; also elsewhere on the board
P2: JP8.32; also elsewhere on the board
P5: JP8.31; also elsewhere on the board
P6: JP8.29; also elsewhere on the board
P7: JP8.27; also elsewhere on the board
P8: JP8.25; also elsewhere on the board
P9: JP8.42; also elsewhere on the board
P10: JP8.41; also elsewhere on the board
P11: JP8.43; also elsewhere on the board
P12: JP8.37; also elsewhere on the board
P14: JP8.38; also elsewhere on the board
P15: JP8.40; also elsewhere on the board
P16: JP8.39; also elsewhere on the board
P17: JP8.44; also elsewhere on the board
P21: JP8.46; also elsewhere on the board
P22: JP8.48; also elsewhere on the board
P23: JP8.45; also elsewhere on the board
P35: JP8.47; also elsewhere on the board
P38: JP7.29; also elsewhere on the board
P66: JP7.26; also elsewhere on the board
P67: JP7.24; also elsewhere on the board
P74: JP7.34; also elsewhere on the board
P75: JP7.33; also elsewhere on the board
P78: JP7.28; also elsewhere on the board
P79: JP7.27; also elsewhere on the board
P80: JP7.25; also elsewhere on the board
P81: JP7.23; also elsewhere on the board
P82: JP7.21; also elsewhere on the board
P83: JP7.14; also elsewhere on the board
P84: JP7.17; also elsewhere on the board
P85: JP7.15; also elsewhere on the board
P87: JP7.16; also elsewhere on the board
P88: JP7.13; also elsewhere on the board
P92: JP7.12; also elsewhere on the board
P93: JP7.10; also elsewhere on the board
P94: JP7.9; also elsewhere on the board
P95: JP7.8; also elsewhere on the board
P97: JP7.11; also elsewhere on the board
P98: JP7.7; also elsewhere on the board
P99: JP7.6; also elsewhere on the board
P100: JP7.5; also elsewhere on the board
P101: JP7.4; also elsewhere on the board
P102: JP7.3; also elsewhere on the board
P104: JP7.1; also elsewhere on the board
P105: JP7.2; also elsewhere on the board
P111: JP7.19; also elsewhere on the board
P112: JP7.18; also elsewhere on the board
P114: JP7.20; also elsewhere on the board
P115: JP7.22; also elsewhere on the board
P116: JP7.31; also elsewhere on the board
P117: JP7.32; also elsewhere on the board
P118: JP7.30; also elsewhere on the board
P119: JP8.23; also elsewhere on the board
P120: JP8.21; also elsewhere on the board
P134: JP8.17; also elsewhere on the board
P137: JP8.19; also elsewhere on the board
P138: JP8.18; also elsewhere on the board
P139: JP8.20; also elsewhere on the board
P140: JP8.22; also elsewhere on the board
P141: JP8.24; also elsewhere on the board
P142: JP8.26; also elsewhere on the board
P143: JP8.28; also elsewhere on the board
PA0: JP7.48; also elsewhere on the board
PA1: JP7.47; also elsewhere on the board
PA2: JP7.46; also elsewhere on the board
PA3: JP7.45; also elsewhere on the board
PA4: JP7.44; also elsewhere on the board
PA5: JP7.43; also elsewhere on the board
PA6: JP7.42; also elsewhere on the board
PA7: JP7.41; also elsewhere on the board
PA8: JP8.58; also elsewhere on the board
PA9: JP8.57; also elsewhere on the board
PA10: JP8.60; also elsewhere on the board
PB4: JP7.63; also elsewhere on the board
PB5: JP7.64; also elsewhere on the board
PB6: JP7.61; also elsewhere on the board
PB8: JP7.62; also elsewhere on the board
PB9: JP7.59; also elsewhere on the board
PB10: JP8.52; also elsewhere on the board
PB11: JP8.51; also elsewhere on the board
PC0: JP7.54; also elsewhere on the board
PC1: JP7.53; also elsewhere on the board
PC2: JP7.52; also elsewhere on the board
PC3: JP7.51; also elsewhere on the board
PC4: JP7.50; also elsewhere on the board
PC5: JP7.49; also elsewhere on the board
PC6: JP8.54; also elsewhere on the board
PC7: JP8.53; also elsewhere on the board
PC8: JP8.56; also elsewhere on the board
PC9: JP8.55; also elsewhere on the board
PC10: JP8.62; also elsewhere on the board
PC11: JP8.61; also elsewhere on the board
PC12: JP8.64; also elsewhere on the board
PD2: JP8.63; also elsewhere on the board
PD12: JP8.50; also elsewhere on the board
PD13: JP8.49; also elsewhere on the board
PE2: JP7.60; also elsewhere on the board
PE3: JP7.57; also elsewhere on the board
PE4: JP7.58; also elsewhere on the board
PE5: JP7.55; also elsewhere on the board
PE6: JP7.56; also elsewhere on the board
REFA: JP8.14; also elsewhere on the board
REF_SEL: JP8.13; also elsewhere on the board
VA0: JP8.2; also elsewhere on the board
VA1: JP8.1; also elsewhere on the board
VA2: JP8.4; also elsewhere on the board
VA3: JP8.3; also elsewhere on the board
VA4: JP8.6; also elsewhere on the board
VA5: JP8.5; also elsewhere on the board
VB0: JP8.11; also elsewhere on the board
VB1: JP8.12; also elsewhere on the board
VB2: JP8.9; also elsewhere on the board
VB3: JP8.10; also elsewhere on the board
VB4: JP8.7; also elsewhere on the board
VB5: JP8.8; also elsewhere on the board
VCC: JP8.33, JP8.34; also elsewhere on the board
VREF: JP7.39; also elsewhere on the board

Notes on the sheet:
Connectors
(T2.1/T5.1/ADC0)
(T2.2/T5.2/ADC1)
(T9.1/ADC2)
(T9.2/ADC3)
(ADC10)
(ADC11)
(ADC12)
(ADC13)
(ADC14)
(ADC15)
(I2C1 SCL)
(I2C1 SDA)
(UART1 Tx)
(T3.1)
(T3.2)
(UART5 Rx)
(UART5 Tx)
(T8.1/T3.1/U6 Tx)
(T8.2/T3.2/U6 Rx)
(T8.3/T3.3/U6 Ck)
(T8.4/T3.4)
(T4.2)
(T4.1)
(U1 Tx/T1.2)
(U1 Rx/T1.3)
(U1 Ck/T1.1)
(U3 Tx/U4 Tx)
(U3 Rx/U4 Rx)
(I2C2 SDA/U3 Rx)
(I2C2 SCL/U3 Tx)
12x ADC
39x STM32
62x FPGA


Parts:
IC1: STM32F10XVXT6; TQFP100
JP2: CORTEX_JTAGS; 2X05SMD
Q3: 25.000; XO53
R14: 100k; R0603
R15: 10k; R0603
S2: Reset; B3F-10XX-SMD

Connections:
!RESET: IC1.14 (NRST), JP2.10 (!RESET), R15.1, S2.P1 (S)
!SD_CS: IC1.58 (PD11); also elsewhere on the board
+3V3: JP2.1 (VREF), Q3.4 (VCC), R15.2; also elsewhere on the board
CCLK: IC1.35 (PB0); also elsewhere on the board
DONE: IC1.7 (PC13); also elsewhere on the board
FSMC_CLK: IC1.84 (PD3); also elsewhere on the board
FSMC_D0: IC1.61 (PD14); also elsewhere on the board
FSMC_D1: IC1.62 (PD15); also elsewhere on the board
FSMC_D2: IC1.81 (PD0); also elsewhere on the board
FSMC_D3: IC1.82 (PD1); also elsewhere on the board
FSMC_D4: IC1.38 (PE7); also elsewhere on the board
FSMC_D5: IC1.39 (PE8); also elsewhere on the board
FSMC_D6: IC1.40 (PE9); also elsewhere on the board
FSMC_D7: IC1.41 (PE10); also elsewhere on the board
FSMC_D8: IC1.42 (PE11); also elsewhere on the board
FSMC_D9: IC1.43 (PE12); also elsewhere on the board
FSMC_D10: IC1.44 (PE13); also elsewhere on the board
FSMC_D11: IC1.45 (PE14); also elsewhere on the board
FSMC_D12: IC1.46 (PE15); also elsewhere on the board
FSMC_D13: IC1.55 (PD8); also elsewhere on the board
FSMC_D14: IC1.56 (PD9); also elsewhere on the board
FSMC_D15: IC1.57 (PD10); also elsewhere on the board
FSMC_NADV: IC1.93 (PB7); also elsewhere on the board
FSMC_NBL0: IC1.97 (PE0); also elsewhere on the board
FSMC_NBL1: IC1.98 (PE1); also elsewhere on the board
FSMC_NE1: IC1.88 (PD7); also elsewhere on the board
FSMC_NOE: IC1.85 (PD4); also elsewhere on the board
FSMC_NWAIT: IC1.87 (PD6); also elsewhere on the board
FSMC_NWE: IC1.86 (PD5); also elsewhere on the board
GND: JP2.3 (GND), JP2.5 (GND), JP2.9 (GNDDETECT), Q3.2 (GND), R14.1, S2.P4 (P1); also elsewhere on the board
INIT_B: IC1.36 (PB1); also elsewhere on the board
unnamed: IC1.94 (BOOT0), R14.2
unnamed: IC1.12 (OSC_IN), Q3.3 (OUT)
PA0: IC1.23 (PA0); also elsewhere on the board
PA1: IC1.24 (PA1); also elsewhere on the board
PA2: IC1.25 (PA2); also elsewhere on the board
PA3: IC1.26 (PA3); also elsewhere on the board
PA4: IC1.29 (PA4); also elsewhere on the board
PA5: IC1.30 (PA5); also elsewhere on the board
PA6: IC1.31 (PA6); also elsewhere on the board
PA7: IC1.32 (PA7); also elsewhere on the board
PA8: IC1.67 (PA8); also elsewhere on the board
PA9: IC1.68 (PA9); also elsewhere on the board
PA10: IC1.69 (PA10); also elsewhere on the board
PB4: IC1.90 (PB4); also elsewhere on the board
PB5: IC1.91 (PB5); also elsewhere on the board
PB6: IC1.92 (PB6); also elsewhere on the board
PB8: IC1.95 (PB8); also elsewhere on the board
PB9: IC1.96 (PB9); also elsewhere on the board
PB10: IC1.47 (PB10); also elsewhere on the board
PB11: IC1.48 (PB11); also elsewhere on the board
PC0: IC1.15 (PC0); also elsewhere on the board
PC1: IC1.16 (PC1); also elsewhere on the board
PC2: IC1.17 (PC2); also elsewhere on the board
PC3: IC1.18 (PC3); also elsewhere on the board
PC4: IC1.33 (PC4); also elsewhere on the board
PC5: IC1.34 (PC5); also elsewhere on the board
PC6: IC1.63 (PC6); also elsewhere on the board
PC7: IC1.64 (PC7); also elsewhere on the board
PC8: IC1.65 (PC8); also elsewhere on the board
PC9: IC1.66 (PC9); also elsewhere on the board
PC10: IC1.78 (PC10); also elsewhere on the board
PC11: IC1.79 (PC11); also elsewhere on the board
PC12: IC1.80 (PC12); also elsewhere on the board
PD2: IC1.83 (PD2); also elsewhere on the board
PD12: IC1.59 (PD12); also elsewhere on the board
PD13: IC1.60 (PD13); also elsewhere on the board
PE2: IC1.1 (PE2); also elsewhere on the board
PE3: IC1.2 (PE3); also elsewhere on the board
PE4: IC1.3 (PE4); also elsewhere on the board
PE5: IC1.4 (PE5); also elsewhere on the board
PE6: IC1.5 (PE6); also elsewhere on the board
PROGRAM_B: IC1.37 (BOOT1/PB2); also elsewhere on the board
SD_DETECT: IC1.9 (PC15); also elsewhere on the board
SPI2_MISO: IC1.53 (PB14); also elsewhere on the board
SPI2_MOSI: IC1.54 (PB15); also elsewhere on the board
SPI2_NSS: IC1.51 (PB12); also elsewhere on the board
SPI2_SCK: IC1.52 (PB13); also elsewhere on the board
TCK: IC1.76 (PA14), JP2.4 (TCK/SWCLK)
TDI: IC1.77 (PA15), JP2.8 (TDI)
TDO: IC1.89 (PB3), JP2.6 (TDO/SWO)
TMS: IC1.72 (PA13), JP2.2 (TMS/SWIO)
USB_DM: IC1.70 (PA11); also elsewhere on the board
USB_DP: IC1.71 (PA12); also elsewhere on the board
USB_VBUS: IC1.8 (PC14); also elsewhere on the board

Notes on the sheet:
(U4 Tx/T2.1/T5.1/ADC0)
(U4 Rx/T2.2/T5.2/ADC1)
(U2 Tx/T9.1/ADC2)
(U2 Rx/T9.2/ADC3)
(T3.1)
(CAN2 Rx/T3.2)
(CAN1 RX)
(CAN1 TX)
(I2C2 SDA/U3 Rx)
(I2C2 SCL/U3 Tx)
(CAN2 Tx)
(U3 Tx/U4 Tx)
(U3 Rx/U4 Rx)
(UART5 Rx)
STM32
Encoder at T1..5 and T8
(ADC10)
(ADC11)
(ADC12)
(ADC13)
(ADC14)
(ADC15)
(T8.1/T3.1)
(T8.2/T3.2)
(T8.3/T3.3)
(T8.4/T3.4)
PC13..15 only as Inputs!
(UART5 Tx)
(A18/T4.2)
(A17/T4.1)
(A16)
(A23)
(A19)
(A20)
(A21)
(A22)
(U1 Tx/T1.2)
(U1 Rx/T1.3)
(SPI1 CS)
(SPI1 SCK)

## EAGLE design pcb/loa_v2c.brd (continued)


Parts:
JP3: ML10S
Q2: 50.000; XO53
R4, R11: 330; R0603
R7: 10k; R0603
RN3, RN4, RN6, RN7: 33; EXB38V
U1: 6SLX9TQG144; TQ144

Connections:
!ADC_CS: U1.P126 (IO_L36N_GCLK14_0); also elsewhere on the board
+3V3: JP3.2, Q2.4 (VCC), R4.2, R11.2, U1.P4 (VCCO_3), U1.P18 (VCCO_3), U1.P31 (VCCO_3), U1.P42 (VCCO_2), U1.P60 (IO_L13P_M1_2), U1.P63 (VCCO_2), U1.P76 (VCCO_1), U1.P86 (VCCO_1), U1.P103 (VCCO_1), U1.P122 (VCCO_0), U1.P125 (VCCO_0), U1.P135 (VCCO_0); also elsewhere on the board
ADC_A0: U1.P127 (IO_L36P_GCLK15_0); also elsewhere on the board
ADC_A1: U1.P131 (IO_L35N_GCLK16_0); also elsewhere on the board
ADC_A2: U1.P132 (IO_L35P_GCLK17_0); also elsewhere on the board
ADC_CLK: U1.P124 (IO_L37P_GCLK13_0); also elsewhere on the board
ADC_DOUTA: U1.P121 (IO_L62P_0); also elsewhere on the board
ADC_DOUTB: U1.P123 (IO_L37N_GCLK12_0); also elsewhere on the board
ADC_SGL_DIFF: U1.P133 (IO_L34N_GCLK18_0); also elsewhere on the board
CCLK: U1.P70 (IO_L1P_CCLK_2); also elsewhere on the board
DONE: R11.1, U1.P71 (DONE_2); also elsewhere on the board
FPGA_CLK: Q2.3 (OUT), U1.P55 (IO_L30N_GCLK0_USERCCLK_2)
FPGA_TCK: JP3.6, U1.P109 (TCK)
FPGA_TDI: JP3.10, U1.P110 (TDI)
FPGA_TDO: JP3.8, U1.P106 (TDO)
FPGA_TMS: JP3.4, U1.P107 (TMS)
FSMC_CLK: U1.P24 (IO_L41P_GCLK27_3); also elsewhere on the board
FSMC_D0: RN3.4 (1); also elsewhere on the board
FSMC_D1: RN3.3 (1); also elsewhere on the board
FSMC_D2: RN3.2 (1); also elsewhere on the board
FSMC_D3: RN7.2 (1); also elsewhere on the board
FSMC_D4: RN7.1; also elsewhere on the board
FSMC_D5: RN4.4 (1); also elsewhere on the board
FSMC_D6: RN4.3 (1); also elsewhere on the board
FSMC_D7: RN7.3 (1); also elsewhere on the board
FSMC_D8: RN4.2 (1); also elsewhere on the board
FSMC_D9: RN4.1; also elsewhere on the board
FSMC_D10: RN3.1; also elsewhere on the board
FSMC_D11: RN6.4 (1); also elsewhere on the board
FSMC_D12: RN6.3 (1); also elsewhere on the board
FSMC_D13: RN6.2 (1); also elsewhere on the board
FSMC_D14: RN6.1; also elsewhere on the board
FSMC_D15: RN7.4 (1); also elsewhere on the board
FSMC_NADV: U1.P32 (IO_L2N_3); also elsewhere on the board
FSMC_NBL0: U1.P33 (IO_L2P_3); also elsewhere on the board
FSMC_NBL1: U1.P34 (IO_L1N_VREF_3); also elsewhere on the board
FSMC_NE1: U1.P30 (IO_L36P_3); also elsewhere on the board
FSMC_NOE: U1.P27 (IO_L37P_3); also elsewhere on the board
FSMC_NWAIT: U1.P29 (IO_L36N_3); also elsewhere on the board
FSMC_NWE: U1.P26 (IO_L37N_3); also elsewhere on the board
GND: JP3.1, JP3.3, JP3.5, JP3.7, JP3.9, Q2.2 (GND), R7.1, U1.P47 (IO_L48N_RDWR_B_VREF_2), U1.P64 (IO_L3N_MOSI_CSI_B_MISO0_2), U1.P69 (IO_L1N_M0_CMPMISO_2), U1.P73 (SUSPEND); also elsewhere on the board
INIT_B: U1.P39 (IO_L65P_INIT_B_2); also elsewhere on the board
unnamed: RN3.5 (2), U1.P65 (IO_L3P_D0_DIN_MISO_MISO1_2)
unnamed: RN3.6 (2), U1.P62 (IO_L12P_D1_MISO2_2)
unnamed: RN3.7 (2), U1.P61 (IO_L12N_D2_MISO3_2)
unnamed: RN3.8 (2), U1.P59 (IO_L13N_D10_2)
unnamed: RN6.5 (2), U1.P58 (IO_L14P_D11_2)
unnamed: RN6.6 (2), U1.P57 (IO_L14N_D12_2)
unnamed: RN6.7 (2), U1.P56 (IO_L30P_GCLK1_D13_2)
unnamed: RN6.8 (2), U1.P51 (IO_L31P_GCLK31_D14_2)
unnamed: RN7.5 (2), U1.P50 (IO_L31N_GCLK30_D15_2)
unnamed: RN7.6 (2), U1.P48 (IO_L48P_D7_2)
unnamed: RN7.7 (2), U1.P46 (IO_L49P_D3_2)
unnamed: RN7.8 (2), U1.P45 (IO_L49N_D4_2)
unnamed: RN4.5 (2), U1.P44 (IO_L62P_D5_2)
unnamed: R4.1, U1.P144 (IO_L1P_HSWAPEN_0)
unnamed: RN4.7 (2), U1.P41 (IO_L64P_D8_2)
unnamed: RN4.6 (2), U1.P43 (IO_L62N_D6_2)
unnamed: RN4.8 (2), U1.P40 (IO_L64N_D9_2)
P1: U1.P1 (IO_L83N_VREF_3); also elsewhere on the board
P2: U1.P2 (IO_L83P_3); also elsewhere on the board
P5: U1.P5 (IO_L52N_3); also elsewhere on the board
P6: U1.P6 (IO_L52P_3); also elsewhere on the board
P7: U1.P7 (IO_L51N_3); also elsewhere on the board
P8: U1.P8 (IO_L51P_3); also elsewhere on the board
P9: U1.P9 (IO_L50N_3); also elsewhere on the board
P10: U1.P10 (IO_L50P_3); also elsewhere on the board
P11: U1.P11 (IO_L49N_3); also elsewhere on the board
P12: U1.P12 (IO_L49P_3); also elsewhere on the board
P14: U1.P14 (IO_L44N_GCLK20_3); also elsewhere on the board
P15: U1.P15 (IO_L44P_GCLK21_3); also elsewhere on the board
P16: U1.P16 (IO_L43N_GCLK22_IRDY2_3); also elsewhere on the board
P17: U1.P17 (IO_L43P_GCLK23_3); also elsewhere on the board
P21: U1.P21 (IO_L42N_GCLK24_3); also elsewhere on the board
P22: U1.P22 (IO_L42P_GCLK25_TRDY2_3); also elsewhere on the board
P23: U1.P23 (IO_L41N_GCLK26_3); also elsewhere on the board
P35: U1.P35 (IO_L1P_3); also elsewhere on the board
P38: U1.P38 (IO_L65N_CSO_B_2); also elsewhere on the board
P66: U1.P66 (IO_L2N_CMPMOSI_2); also elsewhere on the board
P67: U1.P67 (IO_L2P_CMPCLK_2); also elsewhere on the board
P74: U1.P74 (IO_L74N_DOUT_BUSY_1); also elsewhere on the board
P75: U1.P75 (IO_L74P_AWAKE_1); also elsewhere on the board
P78: U1.P78 (IO_L47N_1); also elsewhere on the board
P79: U1.P79 (IO_L47P_1); also elsewhere on the board
P80: U1.P80 (IO_L46N_1); also elsewhere on the board
P81: U1.P81 (IO_L46P_1); also elsewhere on the board
P82: U1.P82 (IO_L45N_1); also elsewhere on the board
P83: U1.P83 (IO_L45P_1); also elsewhere on the board
P84: U1.P84 (IO_L43N_GCLK4_1); also elsewhere on the board
P85: U1.P85 (IO_L43P_GCLK5_1); also elsewhere on the board
P87: U1.P87 (IO_L42N_GCLK6_TRDY1_1); also elsewhere on the board
P88: U1.P88 (IO_L42P_GCLK7_1); also elsewhere on the board
P92: U1.P92 (IO_L41N_GCLK8_1); also elsewhere on the board
P93: U1.P93 (IO_L41P_GCLK9_IRDY1_1); also elsewhere on the board
P94: U1.P94 (IO_L40N_GCLK10_1); also elsewhere on the board
P95: U1.P95 (IO_L40P_GCLK11_1); also elsewhere on the board
P97: U1.P97 (IO_L34N_1); also elsewhere on the board
P98: U1.P98 (IO_L34P_1); also elsewhere on the board
P99: U1.P99 (IO_L33N_1); also elsewhere on the board
P100: U1.P100 (IO_L33P_1); also elsewhere on the board
P101: U1.P101 (IO_L32N_1); also elsewhere on the board
P102: U1.P102 (IO_L32P_1); also elsewhere on the board
P104: U1.P104 (IO_L1N_VREF_1); also elsewhere on the board
P105: U1.P105 (IO_L1P_1); also elsewhere on the board
P111: U1.P111 (IO_L66N_SCP0_0); also elsewhere on the board
P112: U1.P112 (IO_L66P_SCP1_0); also elsewhere on the board
P114: U1.P114 (IO_L65N_SCP2_0); also elsewhere on the board
P115: U1.P115 (IO_L65P_SCP3_0); also elsewhere on the board
P116: U1.P116 (IO_L64N_SCP4_0); also elsewhere on the board
P117: U1.P117 (IO_L64P_SCP5_0); also elsewhere on the board
P118: U1.P118 (IO_L63N_SCP6_0); also elsewhere on the board
P119: U1.P119 (IO_L63P_SCP7_0); also elsewhere on the board
P120: U1.P120 (IO_L62N_VREF_0); also elsewhere on the board
P134: U1.P134 (IO_L34P_GCLK19_0); also elsewhere on the board
P137: U1.P137 (IO_L4N_0); also elsewhere on the board
P138: U1.P138 (IO_L4P_0); also elsewhere on the board
P139: U1.P139 (IO_L3N_0); also elsewhere on the board
P140: U1.P140 (IO_L3P_0); also elsewhere on the board
P141: U1.P141 (IO_L2N_0); also elsewhere on the board
P142: U1.P142 (IO_L2P_0); also elsewhere on the board
P143: U1.P143 (IO_L1N_VREF_0); also elsewhere on the board
PROGRAM_B: R7.2, U1.P37 (PROGRAM_B_2); also elsewhere on the board

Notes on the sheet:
Done=1 => FPGA configured
ProgramB=0 => FPGA Reset
HSWAP_EN = 0 => internal Pullups during configuration for all pins


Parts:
C9, C45, C46: 100n; C0603
C23, C24: 1µ; C0805
C57, C58: 470n; C0805
IC6: AD7266SU; TQFP32-08
L4: 0,68u; WE-KI_0805_B
R9, R32: 10k; R0603

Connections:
!ADC_CS: IC6.26 (!CS), R32.1; also elsewhere on the board
+3V3: C24.1, C45.1, C46.1, IC6.31 (VDRIVE), IC6.32 (DVDD), L4.1 (2), R32.2; also elsewhere on the board
ADC_A0: IC6.25 (A0); also elsewhere on the board
ADC_A1: IC6.24 (A1); also elsewhere on the board
ADC_A2: IC6.23 (A2); also elsewhere on the board
ADC_CLK: IC6.27 (SCLK); also elsewhere on the board
ADC_DOUTA: IC6.30 (DOUTA); also elsewhere on the board
ADC_DOUTB: IC6.28 (DOUTB); also elsewhere on the board
ADC_SGL_DIFF: IC6.22 (SGL/!DIFF); also elsewhere on the board
AGND: C9.2, C23.2, C57.2, C58.2, IC6.5 (AGND), IC6.6 (AGND), IC6.19 (AGND); also elsewhere on the board
GND: C24.2, C45.2, C46.2, IC6.1 (DGND), IC6.21 (RANGE), IC6.29 (DGND), R9.1; also elsewhere on the board
unnamed: C9.1, C23.1, IC6.3 (AVDD), L4.2 (1)
REFA: C57.1, C58.1, IC6.4 (DCAPA), IC6.20 (DCAPB); also elsewhere on the board
REF_SEL: IC6.2 (REF_SELECT), R9.2; also elsewhere on the board
VA0: IC6.7 (VA1); also elsewhere on the board
VA1: IC6.8 (VA2); also elsewhere on the board
VA2: IC6.9 (VA3); also elsewhere on the board
VA3: IC6.10 (VA4); also elsewhere on the board
VA4: IC6.11 (VA5); also elsewhere on the board
VA5: IC6.12 (VA6); also elsewhere on the board
VB0: IC6.18 (VB1); also elsewhere on the board
VB1: IC6.17 (VB2); also elsewhere on the board
VB2: IC6.16 (VB3); also elsewhere on the board
VB3: IC6.15 (VB4); also elsewhere on the board
VB4: IC6.14 (VB5); also elsewhere on the board
VB5: IC6.13 (VB6); also elsewhere on the board


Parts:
C34, C54, C55: 100n; C0603
C52: 22µ; SMC_C; VOLTAGE 6,3V
C56: 10n; C0603
IC3: AT45DB081D-SU; SO08
JP5: SD_DETECT; SD_MOLEX_49225-0821
LED1, LED2: Red; CHIPLED_0805
LED9: Green; CHIPLED_0805
LED10: Blue; CHIPLED_0805
R1: 820; R0805
R2, R3, R22: 330; R0603
R10: 1M; R0805
R12, R13: 22; R0603
R26, R28, R29: 10k; R0603
X3: MINI-USB; 32005-201

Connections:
!SD_CS: JP5.2 (CD/DAT3), R28.1; also elsewhere on the board
+3V3: C34.1, C52.+, C54.1, C55.1, IC3.3 (RESET), IC3.5 (WP), IC3.6 (VCC), JP5.4 (VDD), LED9.A, R26.2, R28.2, R29.2; also elsewhere on the board
GND: C34.2, C52.-, C54.2, C55.2, C56.2, IC3.7 (GND), JP5.6 (VSS), JP5.SW2, LED1.C, LED2.C, R1.1, R10.1, R22.1, X3.5; also elsewhere on the board
unnamed: LED1.A, R2.1
unnamed: R12.2, X3.2
unnamed: R13.2, X3.3
unnamed: LED2.A, R3.1
unnamed: LED9.C, R22.2
unnamed: LED10.C, R1.2
unnamed: C56.1, R10.2, X3.M1 (S1), X3.M2 (S2), X3.M3 (S3), X3.M4 (S4)
PE5: R2.2; also elsewhere on the board
PE6: R3.2; also elsewhere on the board
SD_DETECT: JP5.SW1; also elsewhere on the board
SPI2_MISO: IC3.8 (SO), JP5.7 (DAT0); also elsewhere on the board
SPI2_MOSI: IC3.1 (SI), JP5.3 (CMD), R26.1; also elsewhere on the board
SPI2_NSS: IC3.4 (CS), R29.1; also elsewhere on the board
SPI2_SCK: IC3.2 (SCK), JP5.5 (CLK); also elsewhere on the board
USB_DM: R12.1; also elsewhere on the board
USB_DP: R13.1; also elsewhere on the board
USB_VBUS: LED10.A, X3.1; also elsewhere on the board

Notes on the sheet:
Storage


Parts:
C6: 22µ; SMC_D; VOLTAGE 20V
C7, C8: 22µ; SMC_C; VOLTAGE 20V
C10, C11, C12, C13: 10n; C0603
C14, C15, C16, C17, C18, C19, C20, C21, C25, C26, C27, C28, C29, C30: 100n; C0603
C47: 4µ7; C0805
C48: 1µ; C0805
CB1: 100n; C0603
CC1: 6n8; C0805
D1: MURS 140; SMB
IC4: MCP1825S-1202E/DB; SOT223
IC5: NCP3170; SO08
L3: 4µ7; L-PISG
R27: 24k9; M0805
R30: 8k06; M0805
RC1: 4k99; M0805
U1: 6SLX9TQG144; TQ144

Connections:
+3V3: C7.+, C8.+, C14.1, C15.1, C16.1, C17.1, C18.1, C19.1, C20.1, C21.1, C25.1, C26.1, C47.1, IC4.1 (IN), L3.2, R27.2, U1.P20 (VCCAUX), U1.P36 (VCCAUX), U1.P53 (VCCAUX), U1.P90 (VCCAUX), U1.P129 (VCCAUX); also elsewhere on the board
GND: C6.-, C7.-, C8.-, C10.2, C11.2, C12.2, C13.2, C14.2, C15.2, C16.2, C17.2, C18.2, C19.2, C20.2, C21.2, C25.2, C26.2, C27.2, C28.2, C29.2, C30.2, C47.2, C48.2, CB1.2, IC4.2 (GND), IC4.4 (GND), IC5.1 (PGND), IC5.3 (AGND), R30.1, RC1.1, U1.P3 (GND), U1.P13 (GND), U1.P25 (GND), U1.P49 (GND), U1.P54 (GND), U1.P68 (GND), U1.P77 (GND), U1.P91 (GND), U1.P96 (GND), U1.P108 (GND), U1.P113 (GND), U1.P130 (GND), U1.P136 (GND); also elsewhere on the board
unnamed: CC1.2, RC1.2
unnamed: CC1.1, IC5.5 (COMP)
unnamed: IC5.8 (VSW), L3.1
unnamed: IC5.4 (FB), R27.1, R30.2
USB_VBUS: D1.A; also elsewhere on the board
VCC: C6.+, CB1.1, D1.C, IC5.2 (VIN), IC5.6 (EN); also elsewhere on the board
VCCINT: C10.1, C11.1, C12.1, C13.1, C27.1, C28.1, C29.1, C30.1, C48.1, IC4.3 (OUT), U1.P19 (VCCINT), U1.P28 (VCCINT), U1.P52 (VCCINT), U1.P89 (VCCINT), U1.P128 (VCCINT)

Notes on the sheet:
35-100mA @ 1,2V
Quiescent Supply Current:
2-12mA @ 3,3V
FPGA Power Supply
PISG 4,7µH => Isat 1.5A
NCP3170A = 500kHZ, NCP3170B = 1MHz


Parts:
C40, C41, C42, C43, C59, C60, C68: 100n; C0603
C61: 4u7; C0805
C62, C64: 1n; C0603
C63, C65: 1µ; C0805
C66, C67: 2u2; C0805
IC1: STM32F10XVXT6; TQFP100
L2: 0,68u; WE-KI_0805_B
SJ1: PDR_ON; SJ_2S
SJ6: SJS

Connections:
+3V3: C40.1, C41.1, C42.1, C43.1, C59.1, C60.1, C61.1, C68.1, IC1.6 (VBAT), IC1.11 (VDD_5), IC1.19 (VSSA), IC1.28 (VDD_4), IC1.50 (VDD_1), IC1.75 (VDD_2), IC1.100 (VDD_3), L2.1 (2), SJ1.3; also elsewhere on the board
GND: C40.2, C41.2, C42.2, C43.2, C59.2, C60.2, C61.2, C66.2, C67.2, C68.2, IC1.10 (VSS_5), IC1.27 (VSS_4), IC1.74 (VSS_2), SJ1.1, SJ6.1; also elsewhere on the board
GNDA: C62.2, C63.2, C64.2, C65.2, IC1.20 (VREF-), SJ6.2; also elsewhere on the board
unnamed: IC1.99 (VSS_3), SJ1.2
unnamed: C62.1, C63.1, IC1.22 (VDDA), L2.2 (1)
unnamed: C66.1, IC1.49 (VSS_1)
unnamed: C67.1, IC1.73 (NC)
VREF: C64.1, C65.1, IC1.21 (VREF+); also elsewhere on the board

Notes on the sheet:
F2: Vcap
F2: RFU
F2: Vdd
F2: VssA
F2: Vcap2
STM32 Power Supply
for STM32F1xx short circuit C38
reserved for future use
for STM32F1xx leave C39 open
F1: GND
F2: open
F4: +3.3V (rev. A)
F4: GND (rev. Z)



Board: 4 copper layers, 42.7 x 72.5 mm, 100 parts (29 on the bottom side), 212 nets.

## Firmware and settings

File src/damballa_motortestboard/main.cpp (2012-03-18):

#include <xpcc/architecture.hpp>
#include <xpcc/workflow.hpp>
#include <xpcc/debug.hpp>

#include "loa/damballa.hpp"
#include "pins.hpp"

#include "uplink.hpp"
#include "fpga.hpp"
#include "led.hpp"
#include "ui.hpp"


xpcc::stm32::Uart5 uart5(115200);
xpcc::IODeviceWrapper<xpcc::stm32::Uart5> loggerDevice(uart5);

// Set all four logger streams to use the UART
xpcc::log::Logger xpcc::log::debug(loggerDevice);
xpcc::log::Logger xpcc::log::info(loggerDevice);
xpcc::log::Logger xpcc::log::warning(loggerDevice);
xpcc::log::Logger xpcc::log::error(loggerDevice);

using namespace xpcc::stm32;

// ----------------------------------------------------------------------------
MAIN_FUNCTION
{
	uart5.configurePins(uart5.REMAP_PC12_PD2);
	
	// Initialize predefined IO-Pins and load the FPGA configuration
	loa::Damballa::initialize();
	
	xpcc::stm32::SysTickTimer::enable();
	
	Uplink::initialize();
	Led::initialize();
	Ui::initialize();
	Fpga::initialize();
	
	XPCC_LOG_INFO << "Motortestboard ready ..." << xpcc::endl;
	
	ColorHsv color = { 0, 255, 100 };
	ColorHsv color2 = { 10, 255, 100 };
	xpcc::PeriodicTimer<> timer(20);
	xpcc::PeriodicTimer<> timer2(500);
	while (1)
	{
		if (timer.isExpired())
		{
			color.hue++;
			color2.hue++;
			
			Led::setHsv(Led::LED1, color);
			Led::setHsv(Led::LED2, color2);
			
			//servo1 = 34150 + (11 - encoder6) * 2845;*/
			//Fpga::setServo(Fpga::SERVO1, servo1);
		}
		
		if (timer2.isExpired())
		{
			loa::Led1::toggle();
			
			uint16_t buttons = Fpga::getButtons() & 0x000f;
			XPCC_LOG_DEBUG << "but=" << buttons << xpcc::endl;
			
			//XPCC_LOG_DEBUG << "l=" << static_cast<int16_t>(Ui::getEncoder(Ui::ENCODER_6) - 12) << xpcc::endl;
			//XPCC_LOG_DEBUG << "r=" << static_cast<int16_t>(Ui::getEncoder(Ui::ENCODER_7) - 12) << xpcc::endl;
			
			//int16_t indexLeft = static_cast<int16_t>(Ui::getEncoder(Ui::ENCODER_6) - 12);
			//int16_t servo1 = indexLeft * 2730;
			
			//XPCC_LOG_DEBUG.printf("servo  =%d\n", servo1);
			//XPCC_LOG_DEBUG.printf("buttons=%04x\n", Ui::button.isPressed(0xffff));

			XPCC_LOG_INFO << "CH0: " << Fpga::getAdc(Fpga::ADC_0);
			XPCC_LOG_INFO << " CH1: " << Fpga::getAdc(Fpga::ADC_1);
			XPCC_LOG_INFO << " CH2: " << Fpga::getAdc(Fpga::ADC_2);
			XPCC_LOG_INFO << " CH3: " << Fpga::getAdc(Fpga::ADC_3);
			XPCC_LOG_INFO << " CH4: " << Fpga::getAdc(Fpga::ADC_4);
			XPCC_LOG_INFO << " CH5: " << Fpga::getAdc(Fpga::ADC_5);
			XPCC_LOG_INFO << " CH6: " << Fpga::getAdc(Fpga::ADC_6);
			XPCC_LOG_INFO << " CH7: " << Fpga::getAdc(Fpga::ADC_7) << xpcc::endl;


			if (Ui::button.isPressed(Ui::BUTTON1))
			{
			}
			
			// set PWM for BLDC2
			//loa::Damballa::writeWord(0x0020, 512 + speed);
		}
		
		Uplink::update();
		Ui::update();
	}
}

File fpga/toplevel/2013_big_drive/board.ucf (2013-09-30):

# All hardware directly situated on the LOA v2b / v2c board

# all IO-Pins are 3.3V
NET "*"			IOSTANDARD = LVCMOS33;

# ----------------------------------------------------------------------------
# Connections to the STM32F407
#?NET "load_p"	LOC = P55;	# PE7
#?NET "reset_n"	LOC = P56;	# PB2 (BOOT0)

# ----------------------------------------------------------------------------
# Connections between stm and fpga

# Clock (connected to a 50 MHz oscillator)
NET "clk"		LOC = P55;
NET "clk"		TNM_NET = clk;
TIMESPEC TS_clk = PERIOD "clk" 50 MHz HIGH 50%;




# ADC (connected via SPI)
NET "ADC_OUT_P_CS_N" 		LOC = P126; # !ADC_CS
NET "ADC_OUT_P_SCK" 		LOC = P124;
NET "ADC_IN_P_D_A" 		LOC = P121;
NET "ADC_IN_P_D_B"		LOC = P123;
NET "ADC_OUT_P_A<0>" 		LOC = P127;
NET "ADC_OUT_P_A<1>" 		LOC = P131;
NET "ADC_OUT_P_A<2>" 		LOC = P132;
NET "ADC_OUT_P_SGL_DIFF"	LOC = P133;



#JTAG:
#SUSPEND	P73
#TCK 		P109
#TDI		P110
#TDO		P106
#TMS		P107


# FSMC
# NET "FSMC_INOUT_P_D<0>"		LOC = P65; # D14
# NET "FSMC_INOUT_P_D<1>"		LOC = P62; # D15
# NET "FSMC_INOUT_P_D<2>"		LOC = P61; # D0
# NET "FSMC_INOUT_P_D<3>"		LOC = P46; # D1
# NET "FSMC_INOUT_P_D<4>"		LOC = P45; # E7
# NET "FSMC_INOUT_P_D<5>"		LOC = P44; # E8
# NET "FSMC_INOUT_P_D<6>"		LOC = P43; # E9
# NET "FSMC_INOUT_P_D<7>"		LOC = P48; # E10
# NET "FSMC_INOUT_P_D<8>"		LOC = P41; # E11
# NET "FSMC_INOUT_P_D<9>"		LOC = P40; # E12
# NET "FSMC_INOUT_P_D<10>"	LOC = P59; # E13
# NET "FSMC_INOUT_P_D<11>"	LOC = P58; # E14
# NET "FSMC_INOUT_P_D<12>"	LOC = P57; # E15
# NET "FSMC_INOUT_P_D<13>"	LOC = P56; # D8
# NET "FSMC_INOUT_P_D<14>"	LOC = P51; # D9
# NET "FSMC_INOUT_P_D<15>"	LOC = P50; # D10

# NET "FSMC_OUT_P_NADV"		LOC = P32; # B7
# NET "FSMC_OUT_P_CLK"		LOC = P24; # D3
# NET "FSMC_OUT_P_NOE"		LOC = P27; # D4
# NET "FSMC_OUT_P_NWE"		LOC = P26; # D5
# NET "FSMC_IN_P_NWAIT"	LOC = P29; # D6
# NET "FSMC_OUT_P_NE1"		LOC = P30; # D7
# NET "FSMC_OUT_P_NBL<0>"		LOC = P33; # E0
# NET "FSMC_OUT_P_NBL<1>"		LOC = P34; # E1

NET "LOAD_P"				LOC = P62;

NET "MOSI_P"		LOC = P56;
NET "MISO_P"		LOC = P51;
NET "SCK_P"		LOC = P50;
NET "CS_NP"		LOC = P65;

# Programming pins, may be used after configuration
# NET "DONE"			LOC = P71; # C13
# NET "PROGRAM_B"		LOC = P37; # B2/Boot1
# NET "INIT_B"		LOC = P39; # B1
# NET "CCLK"			LOC = P70; # B0

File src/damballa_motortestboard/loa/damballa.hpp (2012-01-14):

#ifndef LOA_HPP
#define LOA_HPP

#include <xpcc/architecture.hpp>
#include <xpcc/driver/connectivity/software_spi.hpp>
#include <xpcc/driver/storage/at45db0x1d.hpp>

namespace loa
{
	GPIO__OUTPUT(Led1, E, 3);
	GPIO__OUTPUT(Led2, E, 4);
	GPIO__OUTPUT(Led3, E, 5);
	GPIO__OUTPUT(Led4, E, 6);
	
	typedef xpcc::gpio::Nibble<Led1, Led2, Led3, Led4> Leds;
	
	GPIO__INPUT(Button1, C, 13);
	GPIO__INPUT(Button2, E, 15);
	
	GPIO__OUTPUT(CsFlash, D, 11);
	GPIO__OUTPUT(CsSdCard, D, 3);
	
	/**
	 * USART3 configured as SPI Master
	 * 
	 * TX (MOSI) => PD8
	 * RX (MISO) => PD9
	 * CK (SCLK) => PD10
	 */
	//typedef xpcc::stm32::UsartSpi3 SpiFlash;
	GPIO__OUTPUT(Mosi, D, 8);
	GPIO__INPUT(Miso, D, 9);
	GPIO__OUTPUT(Sck, D, 10);
	
	typedef xpcc::SoftwareSpi<Sck, Mosi, Miso, 40000000> SpiFlash;
	extern SpiFlash spiFlash;
	
	extern xpcc::At45db0x1d<SpiFlash, CsFlash> dataflash;
	
	extern xpcc::stm32::Can1 can;
	
	namespace fpga
	{
		/**
		 * Chip Select during normal operation, DIN during configuration
		 */
		GPIO__OUTPUT(Cs, A, 4);
		extern xpcc::stm32::Spi1 spi;
		
		/**
		 * Driven low during before configuration.
		 * 
		 * After it goes high the M[2:0] pins are sampled and the configuration
		 * is started. Holding the pin low stalls the configuration start.
		 * 
		 * During configuration the FPGA indicates the occurrence of a
		 * configuration data error (i.e., CRC error) by asserting INIT_B Low.
		 * After configuration successfully completes, i.e., when the DONE pin
		 * goes High, the INIT_B pin is available as a full user-I/O pin.
		 */
		GPIO__INPUT(InitB, A, 8);
		
		/**
		 * Load/Store 
		 * 
		 * A rising edge stores the encoder values etc.
		 */
		GPIO__OUTPUT(Load, E, 7);
		
		/**
		 * FPGA Reset
		 * 
		 * Low active. Can be used to reset the internal logic of the FPGA.
		 */
		GPIO__OUTPUT(Reset, B, 2);
		
		// TODO
		GPIO__IO(Unused, E, 2);
	}
	
	// ----------------------------------------------------------------------------
	/**
	 * Peripherals of the Damballa Board
	 * 
	 * 
	 */
	class Damballa
	{
	public:
		/**
		 * Initialize the predefined IO-Pins and load the FPGA configuration
		 */
		static bool
		initialize();
		
		/// Load values into the internal buffers (e.g. encoder values)
		static void
		load();
		
		static void
		writeWord(uint16_t address, uint16_t data);
		
		static uint16_t
		readWord(uint16_t address);
		
		/**
		 * Reloads the FPGA configuration from the dataflash into
		 * the FPGA.
		 * 
		 * \return 	\c true if the configuration was successful loaded.
		 */
		static bool
		reconfigureFpga();
		
	private:
		/// Configure the SPI interface to the FPGA
		static void
		configureSpiFpga();
		/**
		 * Load the configuration into the FPGA
		 */
		static bool
		configureFpga();
		
		/**
		 * Puts the pins used for configuration in an safe state to avoid
		 * drawing constant current over one of the pull-up resistors.
		 */
		static void
		deassertFpgaConfiguration();
	};
}

#endif // LOA_HPP

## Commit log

2011-09-28 Eagle files added
    [cpuboard.brd, cpuboard.sch]
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2011-10-15 New 2mm header for the board connection
    [cpuboard.brd, cpuboard.sch]
2011-10-17 Connectors placed
    [cpuboard.brd, cpuboard.sch]
2011-10-18 IC placed on the board
    [cpuboard.brd, cpuboard.sch]
2011-10-20 Connection between STM32 and FPGA added
    [cpuboard.brd, cpuboard.sch]
2011-10-25 more connections to the STM32
    [cpuboard.brd, cpuboard.sch]
2011-10-27 Named all pins of the STM32, started the documentation of the board
    [cpuboard.brd, cpuboard.sch]
2011-10-27 New layout for the supply pins of the FPGA
    [cpuboard.brd, cpuboard.sch]
2011-11-01 Some more documentation
    [control.brd, control.sch, cpuboard.brd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]
2011-11-02 Initial design for a JTAG programmer which can be used with xc3sprog
    [fpga_programmer.brd, fpga_programmer.sch]
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2011-11-05 First half of the STM32 pins connected and routed
    [control.brd, control.sch]
2011-11-05 Lower part of the board routed
    [control.brd, control.sch]
2011-11-05 Extra plane for the analog ground, supply voltage connections from the datasheet (additional capacitors)
    [control.brd, control.sch]
2011-11-05 Left half of the board routed
    [control.brd, control.sch]
2011-11-05 Finished routing except for the power supply
    [control.brd, control.sch]
2011-11-06 Routing finished, additional LDOs for +5V, 2,5V and 1,2V. +3,3V still needs to be provided externallly
    [control.brd, control.sch]
2011-11-06 Outline for the Power Supply Board, LM4040 as reference voltage added, USB shielding added
    [control.brd, control.sch, control_power.brd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]
2011-11-06 Power Board routed, Position of the board marked in the Reference-Layer
    [control.brd, control_power.brd, control_power.sch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]
2011-11-06 Eagle library for the board
    [control.brd, control.sch, damballah_testboard.brd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]
2011-11-07 Optimized the connector signal assignment, it uses a more natural order now
    [control.brd, control.sch, damballah_testboard.brd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]
2011-11-07 Some minor improvments of the layout, PE2 connected to the FPGA
    [control.brd, control.sch]
2011-11-08 Started a motorcontrol carrier board for damballah
    [damballah_motor.brd, damballah_motor.sch, damballah_testboard.brd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]
2011-11-09 Testboard routing in progress, Added alternative function description to the library
    [damballah_motor.brd, damballah_motor.sch]
2011-11-10 Encoder added to the Testboard
    [damballah_motor.brd, damballah_motor.sch]
2011-11-10 Set part names, Routing WIP
    [control.brd, control.sch, damballah_motor.brd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]
2011-11-14 Motor-Carrier finally completly routed.
    [control.sch, control_power.brd, damballah_2.54mm_adapter.brd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]
2011-11-14 Last changes: Removed ERC Errors, some protection for the ADC
    [control.brd, control.sch, damballah_motor.brd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]
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2011-11-29 Added missing values
    [fpga_programmer.brd, fpga_programmer.sch, loa_carrier_motorcontrol.brd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]
2011-12-09 Testprogram for the new Loa Board
    [fpga_programmer.brd, fpga_programmer.sch, fpga_programmer_r2.brd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]
2011-12-13 - New makefile for the testbenches - New modules: pwm, encoder
    [aiba.brd]
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2011-12-18 Testprogramm for the Damballa Motortestboard
    [project.cfg, stm32f4x.cfg]
2011-12-18 Testbench for the BLDC control module. Generates a strange error from numeric_std
2011-12-18 Changed names of the Hall sensor buses (L1_1 -> LA_1, L2_1 -> LB_1 etc.)
    [loa_carrier_motorcontrol.brd, loa_carrier_motorcontrol.sch]
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2011-12-19 Encoder and Peripheral Register tested. Fixed SpiSlave, MISO was generated one SCK cycle to late and one more cycle was needed for the internal bus before reading bus_i.data after read.
    [damballa.cpp, damballa.hpp, main.cpp]
2011-12-23 Pin 99 needs to be connected to +3.3V for the STM32F4xx
    [loa.sch]
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2012-01-04 Motorcontrolboard extended to control the two BLDC via the rotary encoders
    [loa_carrier_motorcontrol.sch]
2012-01-06 SAB Protocol changed to provide a more reliable communication. Upload retries sending in case of an error.
    [loa_carrier_2.54mm_adapter.sch, loa_carrier_motorcontrol.brd, loa_carrier_motorcontrol.sch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]
2012-01-11 Faster upload (~9 KiB/s) via serial due to bigger packets (256 byte payload)
    [project.cfg]
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2012-03-29 New project for the 2012 robot
    [loa.sch]
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2012-04-13 [bake] Ultrasonic Transmitter Frequency generator with adjustable frequency and fixed deadtime.
    [board.ucf]
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2012-04-18 Current limit fixed for captain. No default values for the break input, otherwise it might be forgotten
2012-04-21 Servo Signals are inverted on the carrier board
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2012-05-22 Limiting values from ADC. Pipeline fixed.
2012-05-24 Current limiter was connected to the wrong motor
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2012-08-17 Ideas for a improved version of the loa board
    [loa_v2.brd, loa_v2.sch]
2012-08-17 Next version with a TQFP100 STM32F4xx because the TQFP144 might be to big
    [loa_v2.brd, loa_v2.sch, loa_v2b.brd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]
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2012-08-18 STM32F407 completley routed, FPGA not finished
    [loa_v2b.brd, loa_v2b.sch]
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2012-08-19 Minor improvments (ground planes etc.)
    [loa_v2b.brd, loa_v2b.sch]
2013-02-05 Added attributes with distributor and order code for most parts of loa_v2b board.
    [loa_v2b.brd, loa_v2b.sch]
2013-02-05 Added some attributes: Order codes.
    [loa_v2b.brd, loa_v2b.sch]
2013-02-07 Added further order codes.
    [loa_v2b.brd, loa_v2b.sch]
2013-02-07 Added even more order codes (sample @Molex).
    [loa_v2b.brd, loa_v2b.sch]
2013-02-08 Modified order codes in attributes again.
    [loa_v2b.brd, loa_v2b.sch]
2013-02-08 Had to change the order codes *again* to adapt to the availability of samples.
    [loa_v2b.brd, loa_v2b.sch]
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2013-02-21 [iMotor] Timer outputs replaced by record.
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2013-02-27 glitch rejection for the UART start bit + loopback example
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2013-03-10 Select correct driver for urjtag and busblaster.
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2013-03-23 FSMC will replace SPI later.
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2013-03-26 Revert commit: SPI Mode 0 fix and add documentation about black magic.
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2013-04-12 Fix UART receive errors.
    For unknown reasons the voter should only examine the middle three bits.
    Even if a framing or parity error is detected the received word is
    written to the FIFO (same behaviour as most micro controllers.)
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2014-05-10 Made files consistent again
    [loa_v2c.brd, loa_v2c.sch]
2014-05-10 New version of the Loa board
    2.54mm pin header, NAND flash added, some minor improvements
    [loa_v3.brd, loa_v3.sch]
2014-05-12 Motor driver with IR21844
    [motor_driver_irf7413.brd, motor_driver_irf7413.sch]
2014-05-21 Changed logo to reflect the version number
    [loa_v3.brd]
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2014-07-18 Update NAND Flash Package, Reduces C type variations
    [loa_v3.brd, loa_v3.sch]
2014-09-26 Fixed DP and DM naming for USB
    [loa_v3.brd, loa_v3.sch]
2015-04-17 Voltage divider added for the V_USB sense pin
    [loa_v3.brd, loa_v3.sch]
2015-11-24 New smaller Loa Board
    - Removed NAND Flash and SD Card
    - Removed 4 ADC and 6 STM32 IOs
    - Removed FPGA Jtag connector (replaced with solder connections)
    - 2x58 instead of 2x64 pins connectors
    [loa_v3.2.brd, loa_v3.2.sch]
